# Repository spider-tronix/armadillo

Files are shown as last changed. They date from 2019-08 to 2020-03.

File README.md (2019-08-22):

# armadillo

Design and control of a wheel capable of varying its radius over a range of values using a novel transformation mechanism. The transformation occurs without any additional actuators. Interestingly the wheel can vary its radius ranging from a large diameter to small diameter which enhances its maneuverability like small turning radius and fast/efficient locomotion.

Skeleton view:

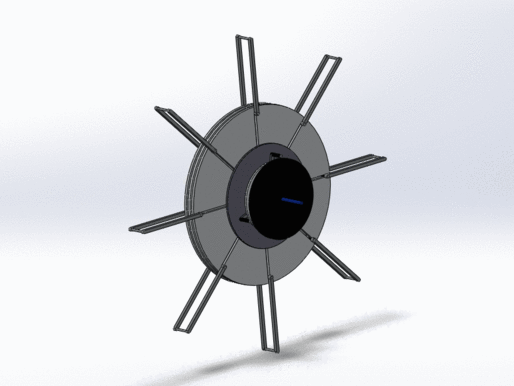
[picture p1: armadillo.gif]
view


Skeleton rear-view:

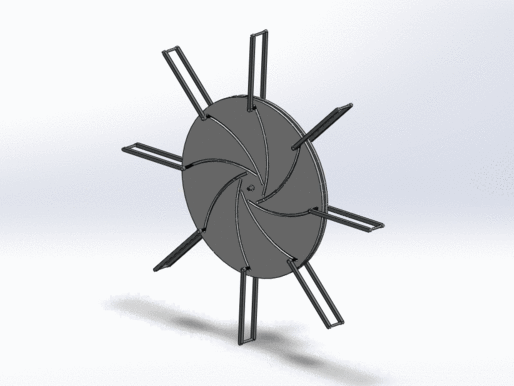
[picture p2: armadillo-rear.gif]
rear-view


The design methodology is explained with much detail in "design.pdf".

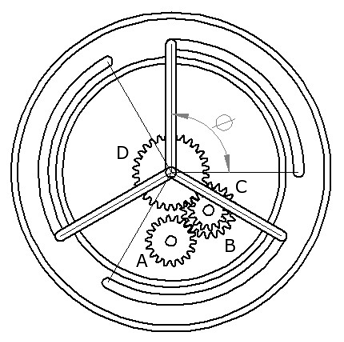
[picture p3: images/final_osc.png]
osc


# Team:
  
  • Mukesh Gandhi [https://github.com/MukkeshGandhi09] 
    
  • Senthur Raj [https://github.com/imsenthur]
  
  • Veejay Karthik [https://github.com/vjkarthik97]
  
  • Soma Karthik [https://github.com/karthiks1701]

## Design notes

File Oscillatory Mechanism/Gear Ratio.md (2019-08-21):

#Oscillatory Mechanism:

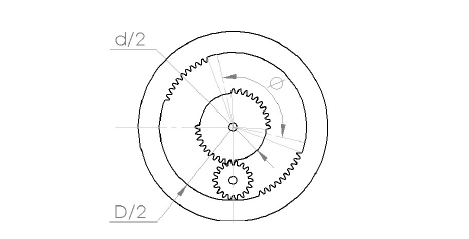
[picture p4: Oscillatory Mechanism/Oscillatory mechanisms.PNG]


The angle of oscillation wrt to inner gear and outer gear is same.

phi*(2d/D-d)=(pi-phi)*(2D/D-d)
phi=pi/(1+(D/d))

    

Ideal Angle of Oscillation
 
Theta=(2d/D-d)*phi
Theta=(2d/D-d)*pi/(1+(D/d))
Theta= 2*pi/(1-k^2)
  
Angle of Oscillation with Clearance 

phi=phi-2*(2*pi/n)
Thetanew= (2/(1-k))*theta
Thetanew=  (2*pi/n)*(n-4(1+k))/(1-k^2)
 
The angle of oscillation is fed to the gear train and Theta max is
obtained

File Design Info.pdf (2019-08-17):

Arc Plate:
Diameter = 160mm
Diameter of arc slots = 3mm
Mass = 63.27 grams
Volume = 63265.19 cubic millimeters
Surface area = 42769.41 square millimeters
Principal axes of inertia and principal moments of inertia: ( grams * square millimeters ) Taken at the center of mass.
Ix = ( 1.00, 0.00, 0.00) | Px = 105645.96
Iy = ( 0.00, 1.00, 0.00) | Py = 105645.96
Iz = ( 0.00, 0.00, 1.00) | Pz = 211162.74
Moments of inertia: ( grams * square millimeters )
Taken at the center of mass and aligned with the output coordinate system. Lxx = 105645.94 Lxy = 0.00 Lxz = 0.00
Lyx = 0.00 Lyy = 105645.97 Lyz = 0.00
Lzx = 0.00 Lzy = 0.00 Lzz = 211162.74
Moments of inertia: ( grams * square millimeters ) Taken at the output coordinate system.
Ixx = 105645.94 Ixy = 0.00 Ixz = 0.00
Iyx = 0.00 Iyy = 105645.97 Iyz = 0.00
Izx = 0.00 Izy = 0.00 Izz = 211162.74

Output shaft:
Diameter = 8mm
Density = 0.00 grams per cubic millimeter Mass = 1.93 grams
Volume = 1926.93 cubic millimeters
Surface area = 1208.18 square millimeters
Principal axes of inertia and principal moments of inertia: ( grams * square millimeters ) Taken at the center of mass.
Ix = ( 0.00, 0.00, 1.00) | Px = 12.45
Iy = ( 0.64, -0.77, 0.00) | Py = 343.81
Iz = ( 0.77, 0.64, 0.00) | Pz = 343.86
Moments of inertia: ( grams * square millimeters )
Taken at the center of mass and aligned with the output coordinate system. Lxx = 343.84 Lxy = -0.02 Lxz = 0.09
Lyx = -0.02 Lyy = 343.84 Lyz = -0.11
Lzx = 0.09 Lzy = -0.11 Lzz = 12.45
Moments of inertia: ( grams * square millimeters ) Taken at the output coordinate system.
Ixx = 3444.88 Ixy = -0.02 Ixz = -0.31
Iyx = -0.02 Iyy = 3444.87 Iyz = 0.38
Izx = -0.31 Izy = 0.38 Izz = 12.45

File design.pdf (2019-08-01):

# Design of a wheel

with dynamically variable curvature.

Rough draft*

Senthur Raj
Department of Production Engineering National Institute of Technology Tiruchirapalli Tamilnadu, India
114116071@nitt.edu

Abstract—This paper presents the design and control of a wheel capable of varying its radius over a range of values using a novel transformation mechanism. The transformation occurs without any additional actuators. Interestingly the wheel can vary its radius ranging from a large diameter to small diameter which enhances its maneuverability like small turning radius and fast/efficient locomotion. Mechanical design of the wheel has been explained in a detailed manner in this paper and also the transforming mechanism and motion study has been shown clearly.
ADD SOME CONTENT HERE

Index Terms—variable radius, maneuverability, locomotion

I. INTRODUCTION

Automobiles are complex machines, in part due to the transmission, suspension,and steering mechanism. By replacing the traditionally static tire with a re-invented wheel that dynamically changes radius, the mechanical complexity of these three systems can be reduced. Reducing the mechanical complexity lowers the cost and required maintenance of a vehicle, all of which are desirable traits for all terrain vehicles and rovers. The design of the wheel consists of three sub-assemblies each of which has dedicated functions to accomplish. The mathematics and working behind each sub-assembly is described in great detail below. INSERT CONTENT HERE !!
Automobiles are complex machines, in part due to the
transmission, | suspension,and | steering | mechanism. | By
replacing the traditionally static tire with a re-invented wheel that dynamically changes radius, the mechanical complexity of these three systems can be reduced. Reducing the mechanical complexity lowers the cost and required maintenance of a vehicle, all of which are desirable traits for all terrain vehicles and rovers. The design of the wheel consists of three sub-assemblies each of which has dedicated functions to accomplish. The mathematics and working behind each sub-assembly is described in great detail below. INSERT CONTENT HERE !!

II. NOMENCLATURE

d | diameter of sun gear
D | diameter of ring gear

D−d
2 | diameter of planet gear

k

d
D
φ | gear mesh angle
n | number of teeth in sun gear
γ | angle of oscillation
θmax | maximum angular displacement of disc
a | radius of inner circle
b | radius of peripheral circle
m | a
| b
A | area of triangle formed by intersection of two circles
L | perimeter of triangle formed by intersection of two circles
r | radial displacement of spokes on wheel
ω | relative angular velocity of disc
t | any instant of time

III. DESIGN METHODOLOGY:
The control of the transformation of wheel is developed in a way to avoid requirement of any additional actuators in order to bring down the hardware complexity. The input shaft when fed with anti-clockwise rotation tends to actuate the transformation mechanism, whereas when fed with clockwise rotation drives the wheel forward. This is type of control over the transformation mechanism is implemented with a trapped one-way bearing,
A. Trapped roller one-way bearing:
A trapped roller one-way bearings is designed to transmit torque between the shaft and housing in one direction and allow free motion in the opposite direction. Proper mounting is easily accomplished with a simple press fit in the casing.

Fig. 1. Trapped roller one-way bearing.

Relative motion between the casing and the input shaft is permitted only when the rotation fed is in clockwise direction. This eliminates any additional actuators required to control the curvature of the wheel.

IV. OSCILLATORY MECHANISM:
The first sub-assembly converts continuous rotation fed in by the input shaft into rotary oscillation of desired angular displacement along the same axis,
A. Gear system that changes direction:

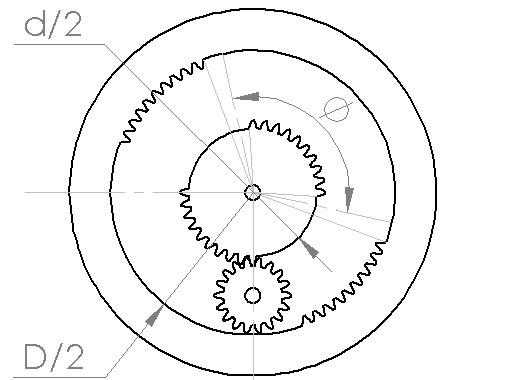
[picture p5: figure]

Fig. 2. Planetary gear assembly.

φ

2d
D−d
= (π −φ)
2D
D−d

φ =

π
(1+k)

(IV-A.1)

B. Angle of oscillation:
The angle of oscillation can be determined as,

γ0 =

2D
D−d
φ

substituting Eq (IV-A.1),

γ0 =

2π
(1−k

2)

the above mentioned angle of oscillation is for an ideal case. While implementation considerations for gear clearance must be made,

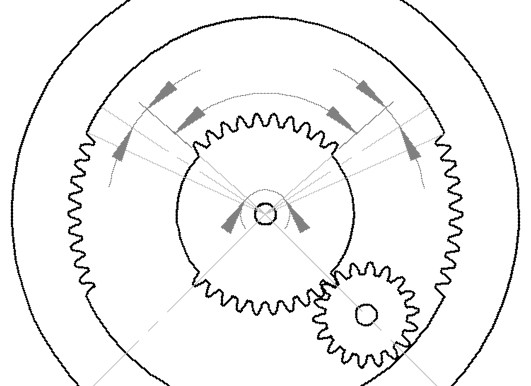
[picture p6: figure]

Fig. 3. Clearance between gears.

therefore, φ = φ −2

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
n−4(1+k)
1−k

2

(IV-B.1)
C. Obtaining the desired angle of oscillation:
The value of θ computed by Eq: (IV-B.1) is completely determined by the ratio of diameters of the sun and ring gears. It is crucial to reduce this value of θ with a gear train in order to reduce the complexity in design of the gear system that changes direction.

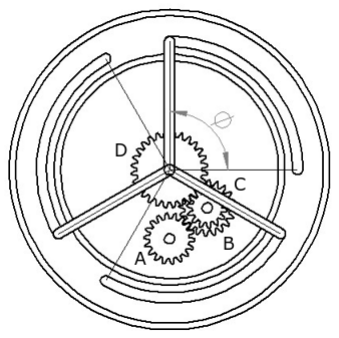
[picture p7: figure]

Fig. 4. Oscillating shaft.

Angle of oscillation of the driver gear (A) is θ which is to be converted into θmax with a compound gear (BC) train with gear ratios,

ratio(AB) =

π

γ

, ratio(CD) =

θmax

π

, ratio(AD) =

θmax

γ

the shaft has three arms, each of which are slotted to prevent overrunning when the driven gear is under clearance angle.

V. EXPANSION MECHANISM:

The expansion mechanism is derived from a self centering mechanism that easily and quickly adjusts to the size of a closed segment ring. This is done by using a pair of disks which rotate against each other, drawing in and out a hex-head nut on a series of opposing arcs. But instead of opposing arcs, the derived system has radial slots in one of the disk opposing the other disc with an arc.

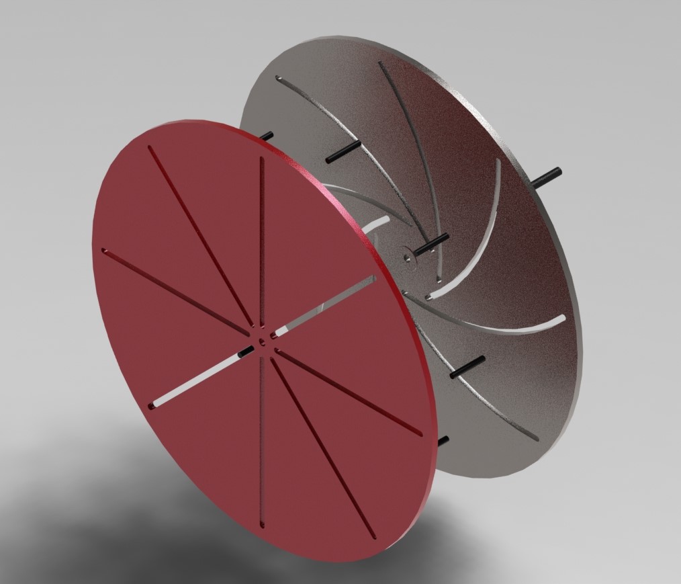
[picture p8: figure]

Fig. 5. Discs and spokes.

A. Locus of the arc:

The arcs on the rotating disc influences the radial expansion of wheel with much impact as they are the driving force behind it. It is important to find their optimal radius of curvature and their corresponding locus assuming center of the shaft as origin.

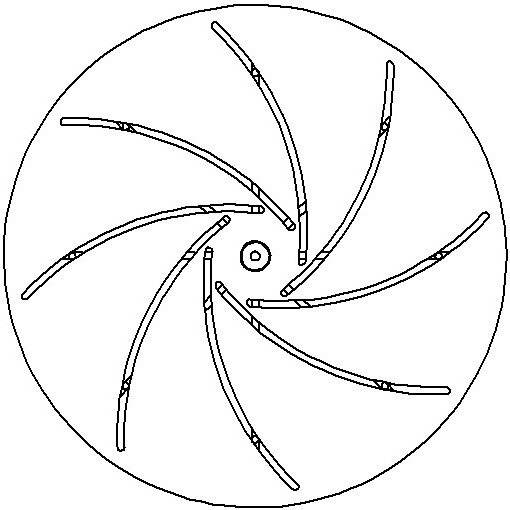
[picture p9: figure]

Fig. 6. arcs.

Locus of the arc is nothing but the intersection of two circles with radii (a + b) and (t) at coordinates (−b,0) and (0,0) respectively. Where (t) is an arbitrary variable.

(x−b)

2 +y

2 = (a+b)

2

x

2 +y

2 | = t
| 2

It is straightforward to show that the intersection of these two circles consists of two points, with the coordinates

x0 =

(−b+0)
2

+

(a+b)

2 −t

2
2L

2

(0−(−b)) +2A
0
L

2

y0 =

(0+0)
2

+

(a+b)

2 −t

2
2L

2

(0) +2A
0−(−b)
L

2

where L is the distance between centers of the two intersecting circles and A is the area of the triangle with edge lengths (a+b), (t), L as given by Herons formula

A =

p
(L+b+a+t)(L+b+a−t)(L+t −b−a)(b+a+t −L) 4

since L = b,

A =

p
(2b+a+t)(2b+a−t)(t −a)(t +a) 4

A =

p
((2b+a)

2 −t

2)(t

2 −a

2)
4

Substituting the values of A and L,

x0 =

−b
2

+

(a+b)

2 −t

2
2b

y0 =

p
((2b+a)

2 −t

2)(t

2 −a

2)
2b

!

Eliminating t, we arrive at locus of the arc,

y

2 | = (a−x)(2b+a+x) | (V-A.1)

where x lies in the domain,
a

2 +2ab−b

| 2
| 2
| <= x <= (a)
B. Polar coordinates:

The locus of arc (Eq:V-A.1) when shifted to polar plane reduces numerous computations during rotation,

x = r cosθ, y = rsinθ

r

2

sin²
θ = (a−r cosθ)(2b+a+r cosθ)

r

2 = 2ab+a 2 −2br cosθ

r =

q
(a+b)

2 −b

2 sin²
θ −bcosθ

where θ lies in the domain,

0 <= θ <= cosh
m

2 +2m−1
2

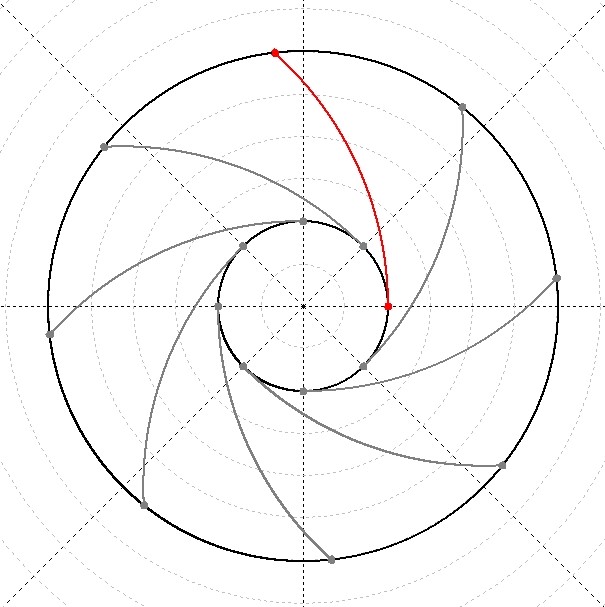
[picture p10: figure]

Fig. 7. Locus of arc.

C. Trajectory of the spoke:

The arcs on the rotating discs determine the curvature of wheel therefore it is crucial to device an equation relating the angular displacement of the disc to the radial expansion of the spokes. Let us consider the trajectory of the spoke which is parallel to x-axis, assuming the spokes are initially at their minimum distance from the origin,

we know that, y = 0 at any point on the trajectory of the above considered spoke and also,

a <= x <= b

Now let us say that the two discs have a relative angular velocity of ω during expansion, at any time t the locus of the arc is given by,

r =

q
(a+b)

2 −b

2 sin²
| (θ −ωt)−bcos(θ −ωt) | (V-C.1)

Trajectory of the spoke in polar coordinates,

rsinθ = 0, | a <= r <= b | (V-C.2)

Computing the intersection of the equations (V-C.1) and (V-C.2) will present us the relationship between the relative angular velocity and the radial expansion of wheel,

rsin(θ −ωt) = 0
=⇒ ωt = θ −nπ

where θ <= cosh
m

2 +2m−1
2
| ,
ωt | = θ

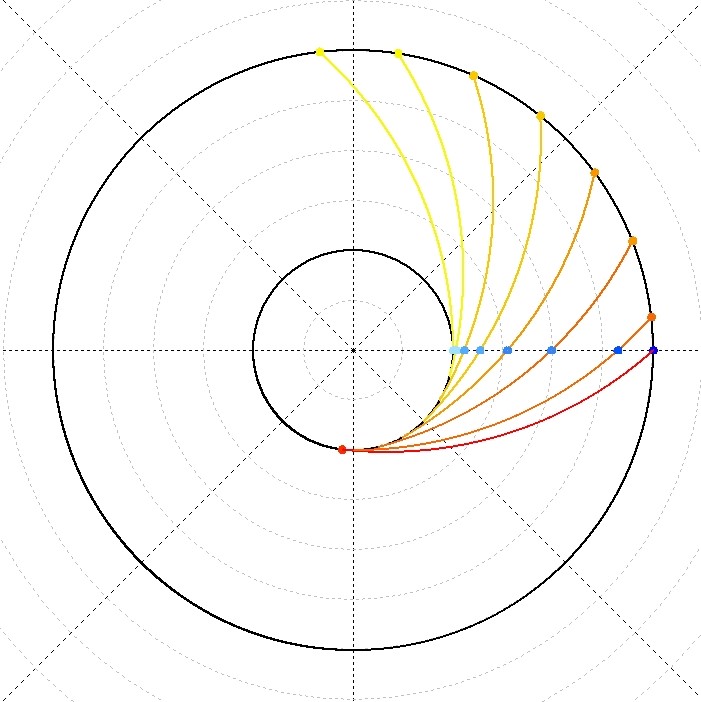
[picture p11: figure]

Fig. 8. Trajectory.

Therefore the angular velocity of the disc and the radial expansion of wheel can be related as,

r =

q
(a+b)

2 −b

2 sin²ωt −bcosωt | (V-C.3)

VI. MOTION STUDY:

A. Rate of expansion:

Now that we have the relationship between angular velocity of the disc and the radial displacement, it is much easier to derive an equation for the rate of expansion. Let us assume at some time t the angular displacement of the disc is θ,

r =

q
(a+b)

2 −b

2 sin²
θ −bcosθ

dr
dt

=

bsinθ −

b

2
cosθ sinθ
q
(a+b)

2 −b
2 sin²
θ

dθ
dt

It is clear that the rate of expansion of the wheel is dependent on the previous state and the angular velocity of the disc.

B. Dependence of ’θmax’ on ’m’:

The dependence of maximum angular displacement of the disc on the ratio of inner and outer radii determines the range over which the curvature of wheel could be varied.
We know that,

θmax = cosh
m

2 +2m−1
2

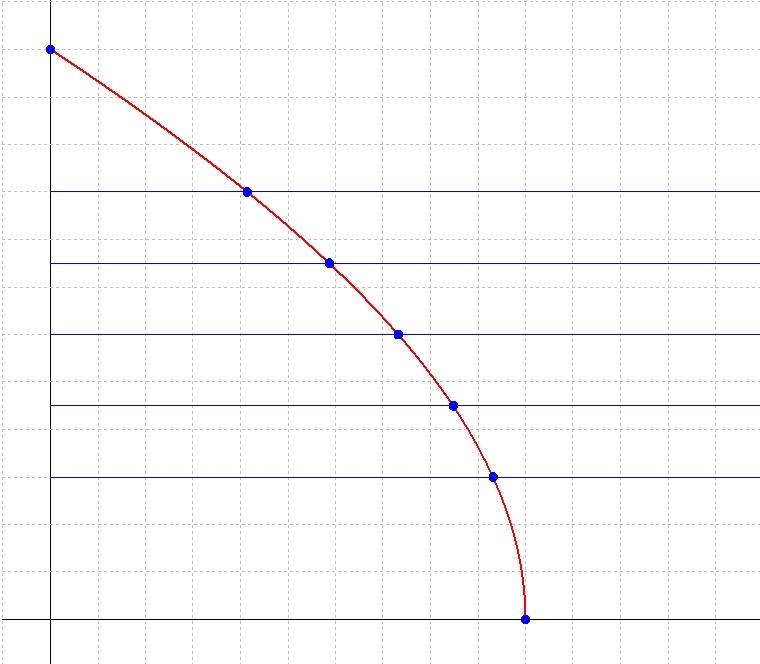
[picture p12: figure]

Fig. 9. θmax vs m.

From the above graph, it is evident that θmax increases with decreasing m, where

0 < m <= 1

also,
−1
2

<

m

2 +2m−1
2

<= 1

0 <= cosh
m

2 +2m−1
2
<

2π
3

=⇒ 0 <= θmax <

2π
3

Therefore θmax ε

0,

2π
3
, though the value of θmax is sub-

jected to change with m it is important to note that it lies well within the constraints posed by the oscillatory mechanism.

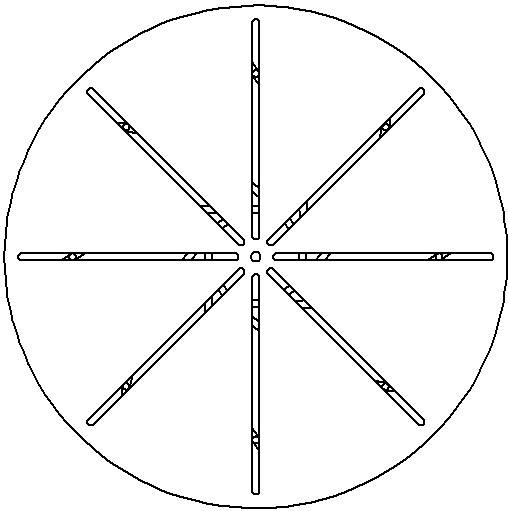
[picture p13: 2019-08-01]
images/faceplate.jpg

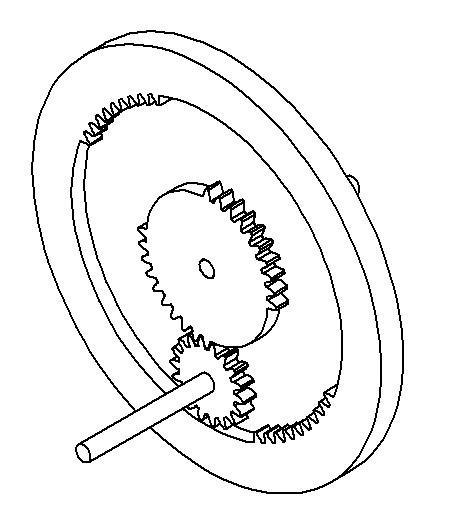
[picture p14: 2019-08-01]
images/mother_child_iso_big.jpg

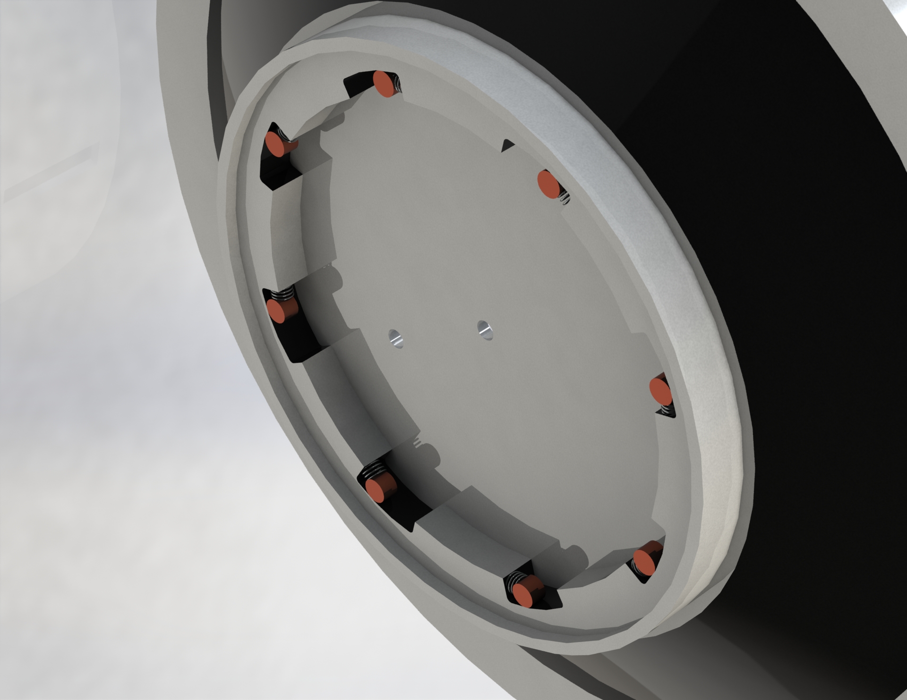
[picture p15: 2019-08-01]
images/trappedRollerBearing.PNG

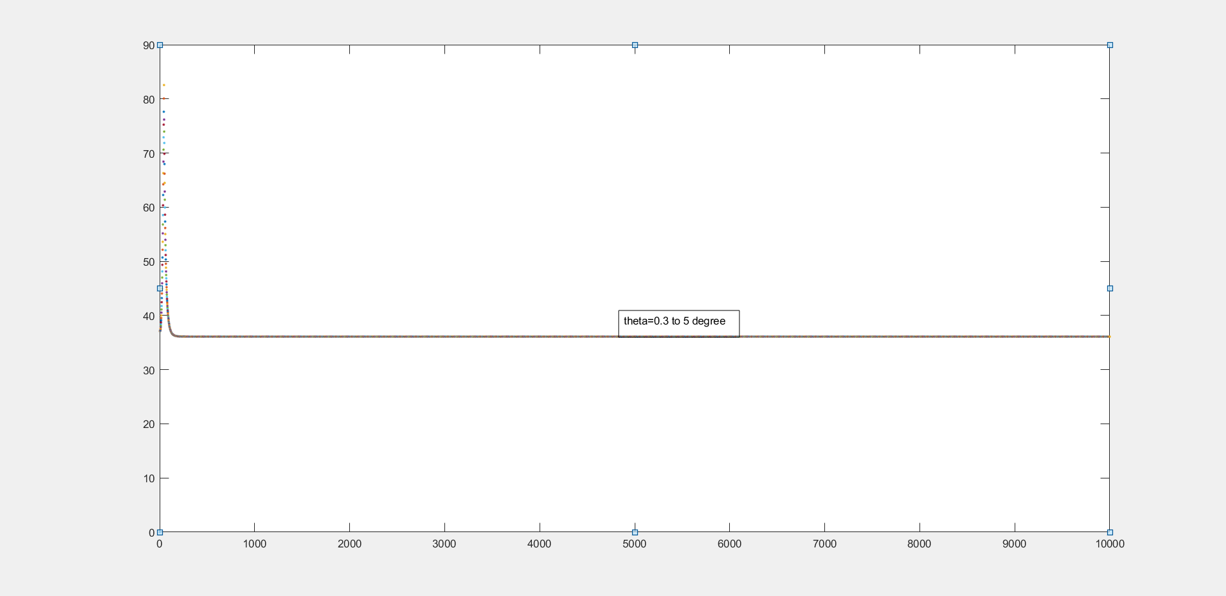
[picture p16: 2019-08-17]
Controller Plots/Higher radius to Lower Radius.png

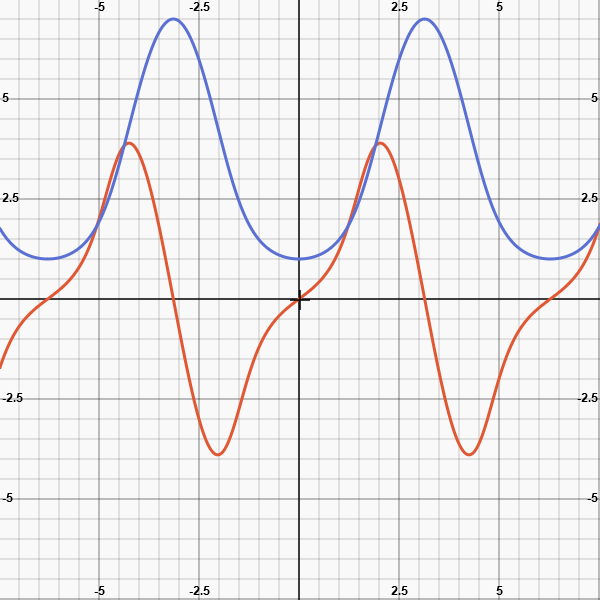
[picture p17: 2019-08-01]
plots/canvas.png

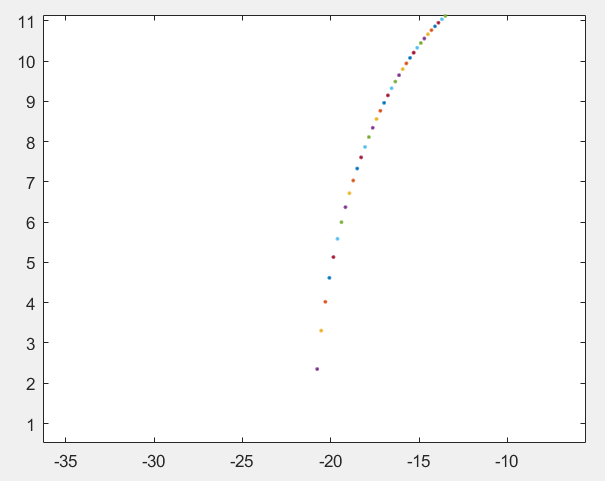
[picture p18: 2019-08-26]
Expansion Mechanism/Plot.PNG

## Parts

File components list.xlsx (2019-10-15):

COMPONENT | REQIREMENT | NO OF PARTS | STATUS
gear box | lasercut | 2 | no
standoff |  |  | no
gear |  | 3 | done
motor |  | 2 | no
coupler |  | 1 | no
gear holder | lasercut | 1 | no
shaft |  | 1
faceplate |  | 1 | done
flange coupling |  | 1 | no
clutch plate |  | 1 | done
spoke |  | 8
idler gear pin |  | 1
actuation shaft |  | 1
casing | 3D print | 1 | no
double bearing | 3D print | 8 | no
bearing |  |  | done
cam | 3D print | 8 | no

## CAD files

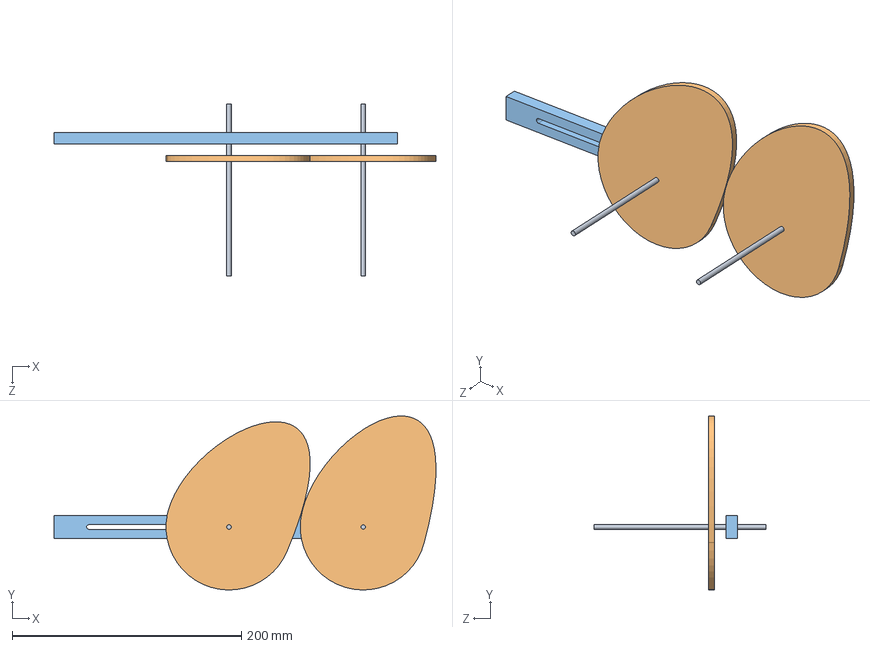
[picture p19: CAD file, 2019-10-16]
new-design/two-spoke-test.SLDASM
333.5 x 151.9 x 150.0 mm
shell-spoke x 2
shell-mockup x 2
mock-spoke-slider

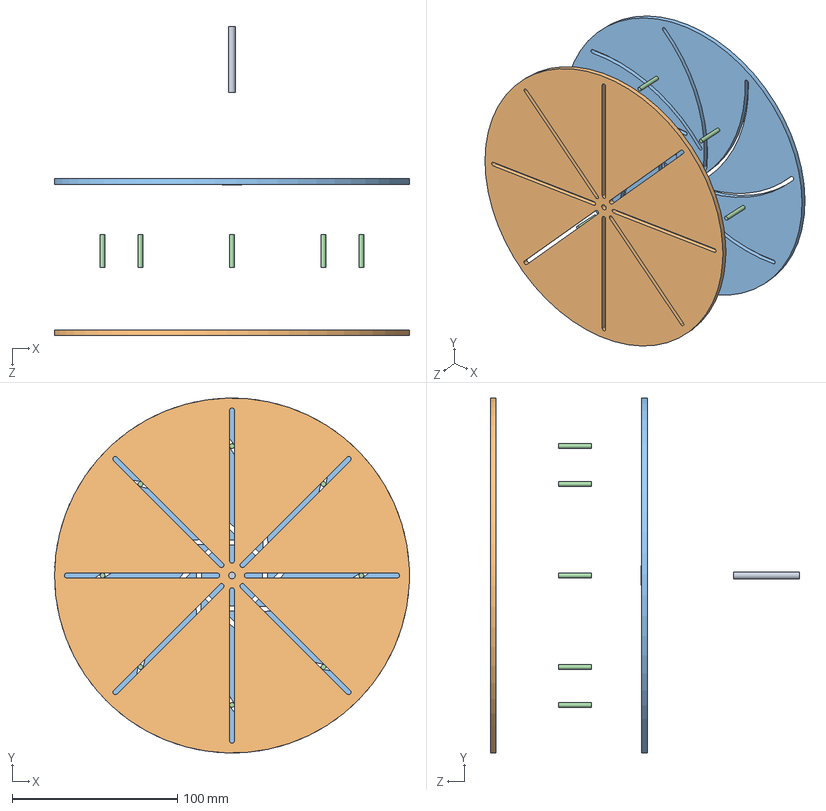
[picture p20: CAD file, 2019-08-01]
subAssemblies/expansion.SLDASM
215.0 x 214.9 x 187.4 mm
shaft_ip
facePlate
clutchPlate
spokes x 8

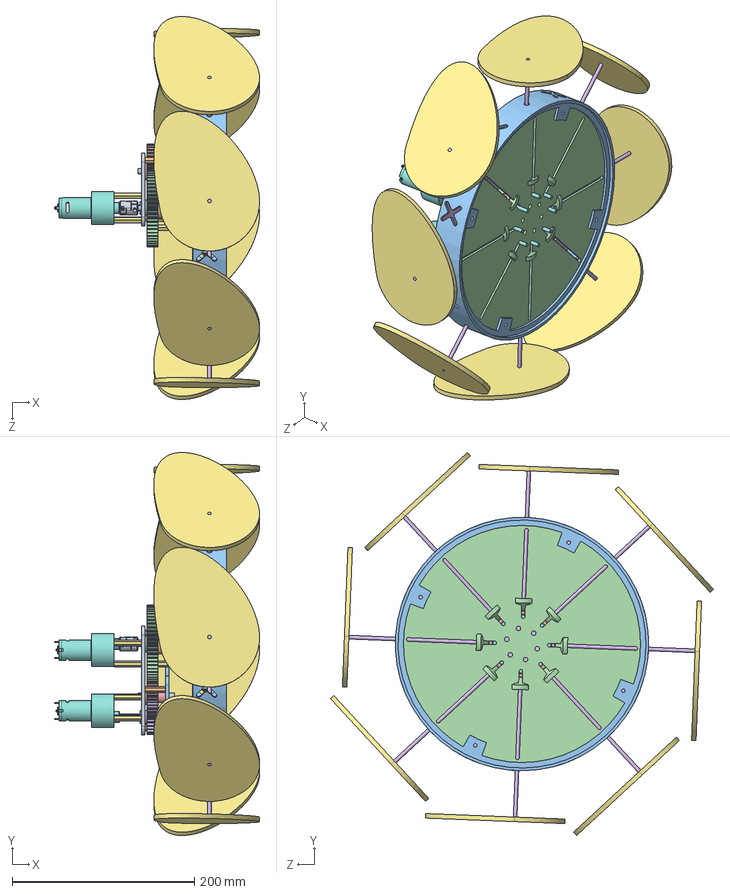
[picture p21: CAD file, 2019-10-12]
new-design/armadillo-assembly.SLDASM
225.1 x 420.1 x 420.1 mm
gear-plate
3mm-standoff x 3
gear-plate-2
56-spur-2
38-spur-2
25-tooth-spur
30mm-3mm-standoff x 6
motor x 2
6mm-coupler
gear-holder
shaft
facePlate-2.0
flange-coupling
clutchPlate-2.0
40MM-3MM-STANDOFF x 3
spoke x 8
idler-gear-pin
actuation-shaft
casing
double-bearing x 8
624RS x 16
shell-spoke x 8
shell-mockup x 8

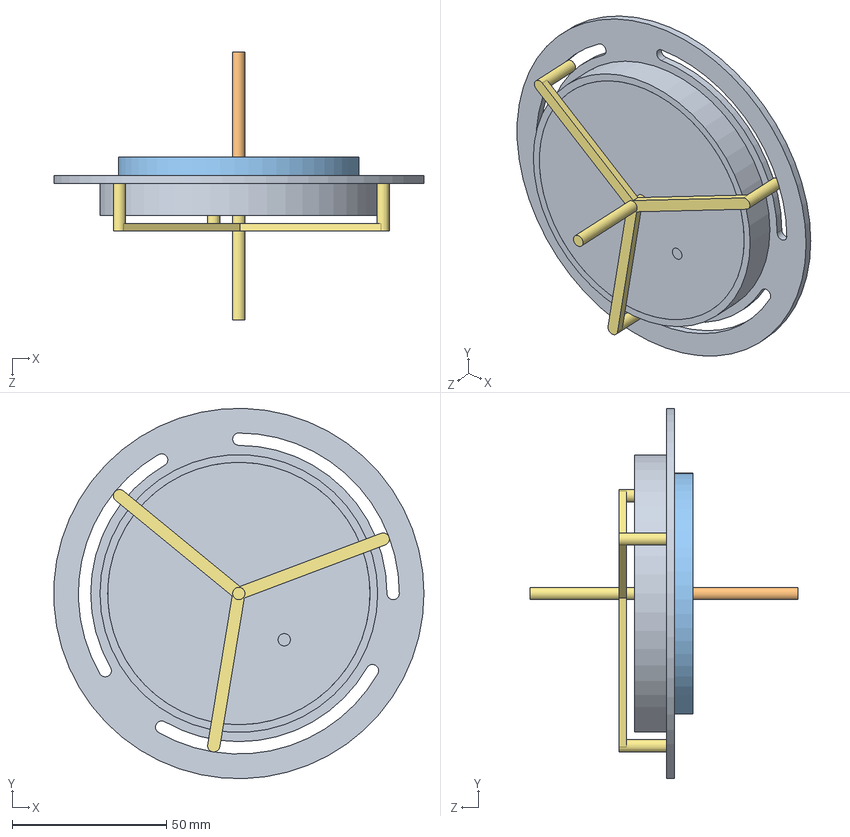
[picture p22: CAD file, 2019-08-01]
subAssemblies/sizeredu_osc_as.SLDASM
119.9 x 119.9 x 86.8 mm
casing
shaft_ip
motherGear_36t72t
childGear_18t x 2
gearPlaceholder
compundGear_20t14t
shaft_op
outSpurGear_28t
enclosingPlate

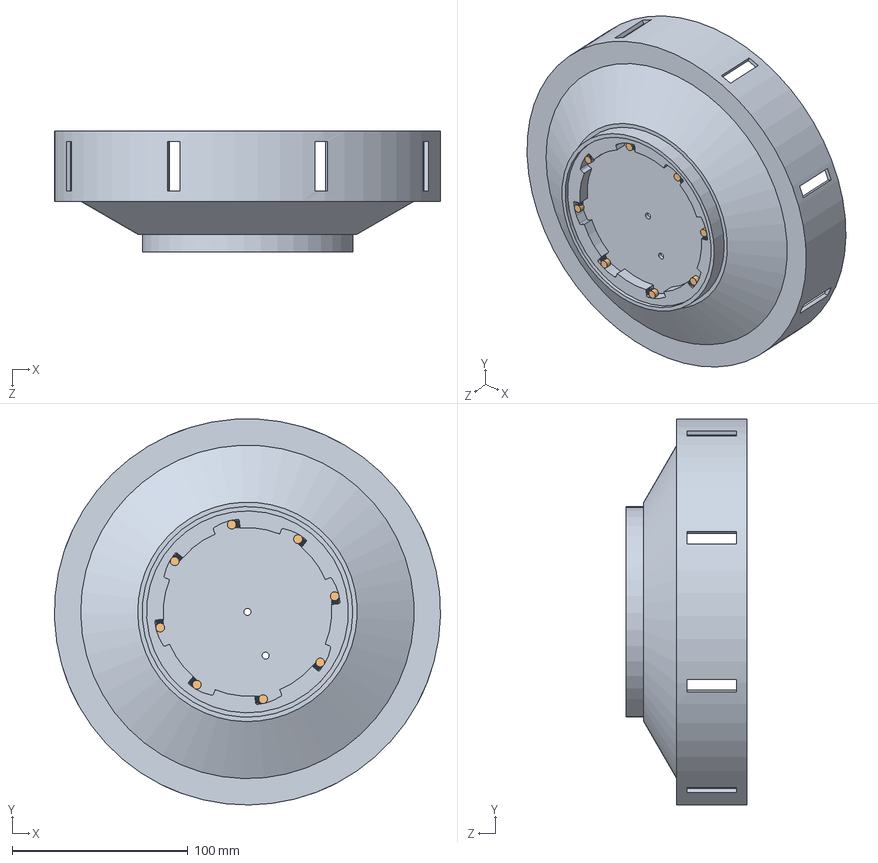
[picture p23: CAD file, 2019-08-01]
subAssemblies/trappedRollerBearing.SLDASM
219.9 x 219.9 x 68.8 mm
casing
trappedRollers x 8
spring x 8

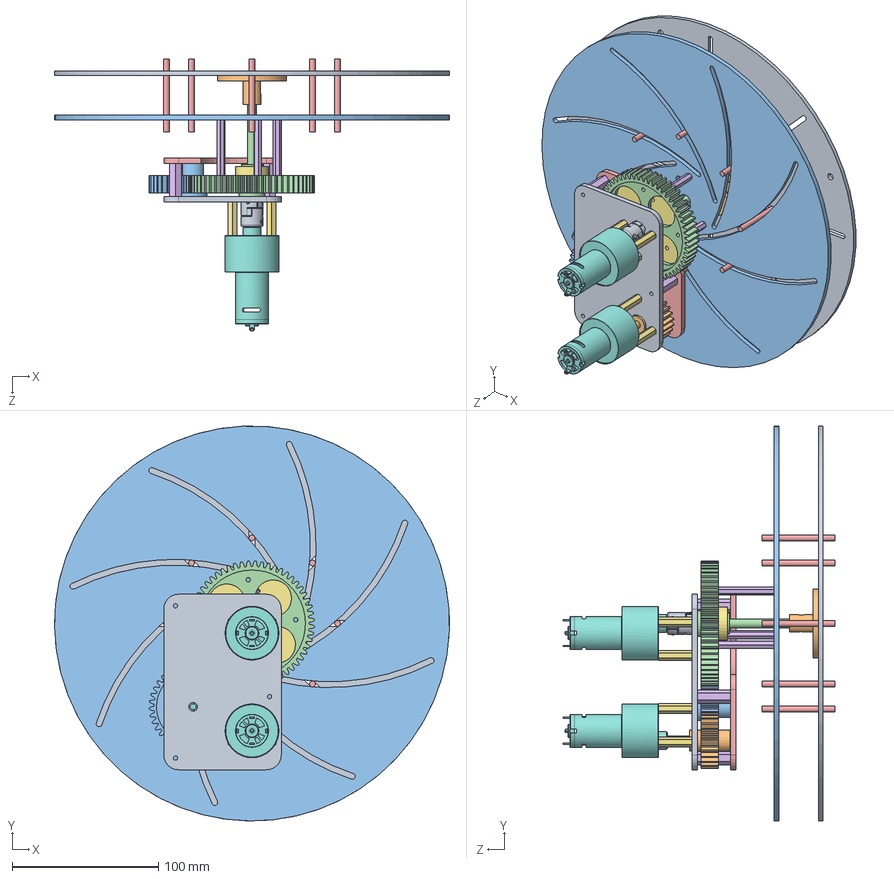
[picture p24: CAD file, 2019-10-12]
new-design/wheel-assembly.SLDASM
270.0 x 269.9 x 186.2 mm
facePlate-2.0
flange-coupling
clutchPlate-2.0
shaft
spoke x 8
TFF-M3x40_DR113.step x 3
gear-holder
idler-gear-pin
gear-plate
25-tooth-spur
38-spur-2
56-spur-2
gear-plate-2
standoff x 3
3mm-standoff x 6
motor x 2
6mm-coupler
actuation-shaft

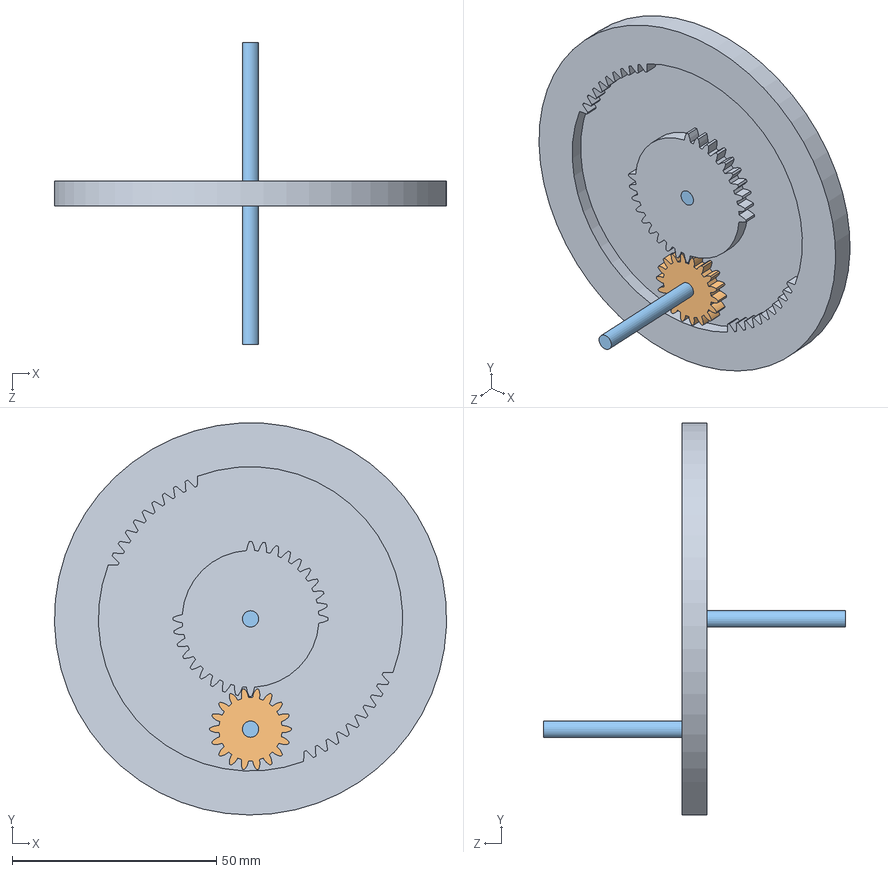
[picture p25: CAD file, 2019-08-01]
subAssemblies/mother_child.SLDASM
96.0 x 95.9 x 74.0 mm
motherGear_36t72t
childGear_18t
shaft_ip x 2

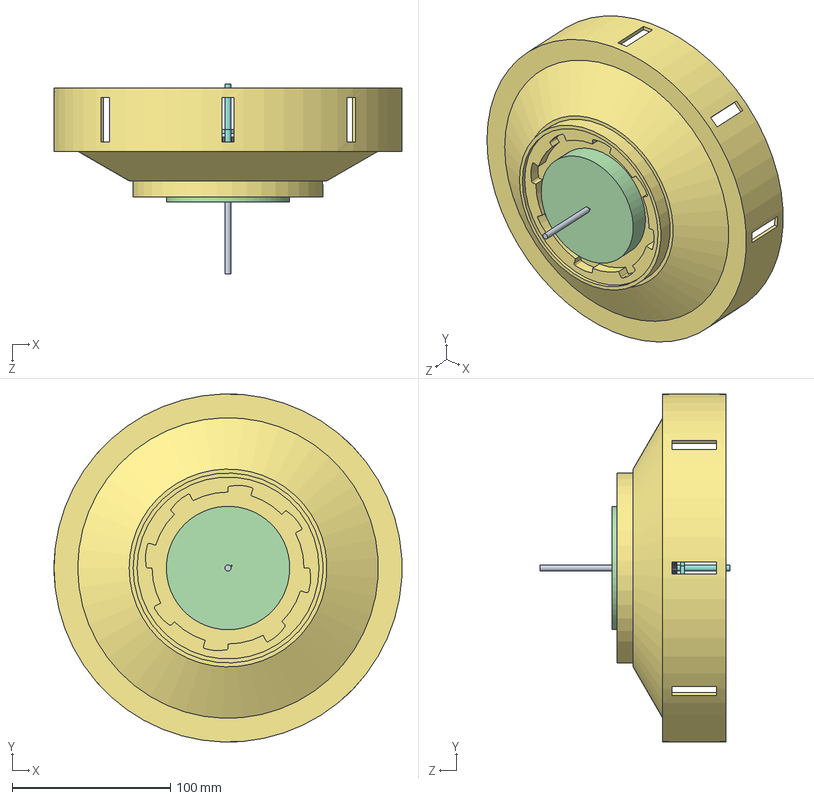
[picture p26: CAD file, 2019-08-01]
subAssemblies/osc_as.SLDASM
219.9 x 219.9 x 120.0 mm
shaft
internalBadassGear x 2
rotationMonitor
mfGear
theOutputGear
theBadassCompoundGear
casing
shaft_op

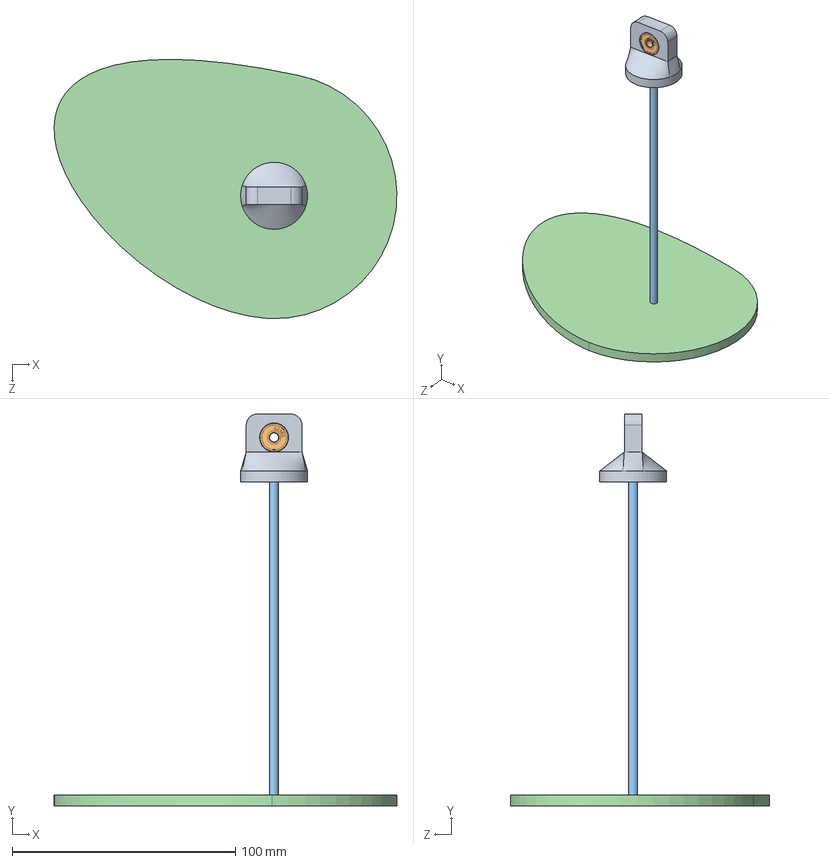
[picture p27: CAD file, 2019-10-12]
new-design/legs.SLDASM
153.5 x 175.5 x 116.1 mm
double-bearing
624RS x 2
shell-spoke
shell-mockup

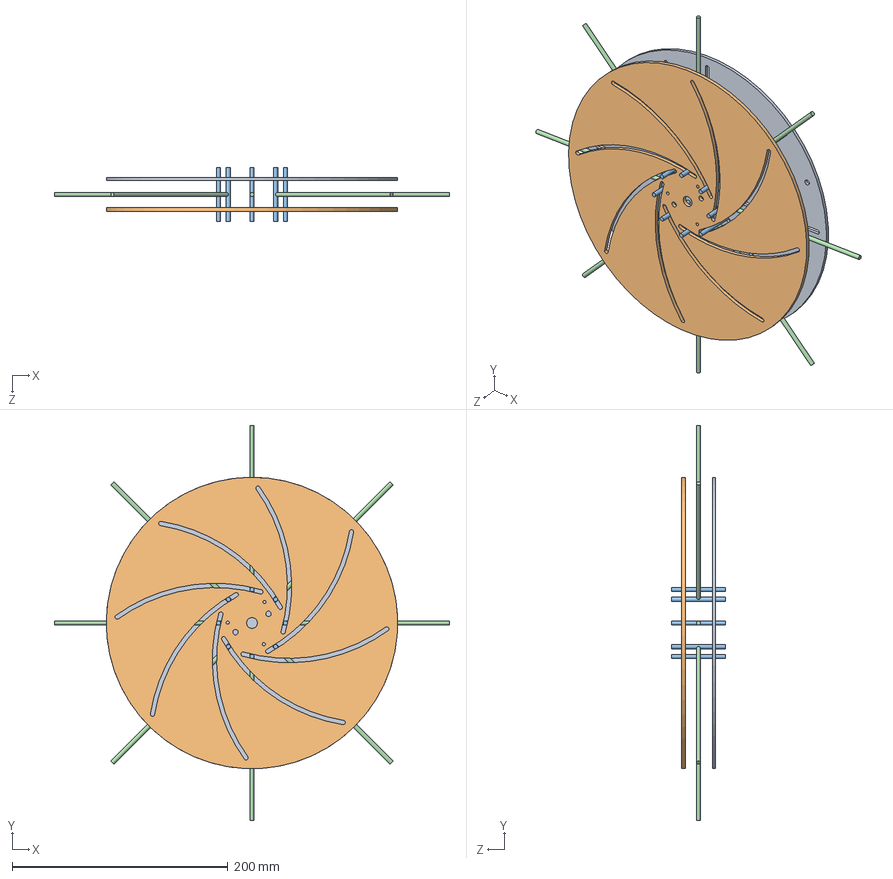
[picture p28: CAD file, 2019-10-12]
new-design/shell-test.SLDASM
365.9 x 365.9 x 50.0 mm
facePlate-2.0
clutchPlate-2.0
spoke x 8
shell-spoke x 8

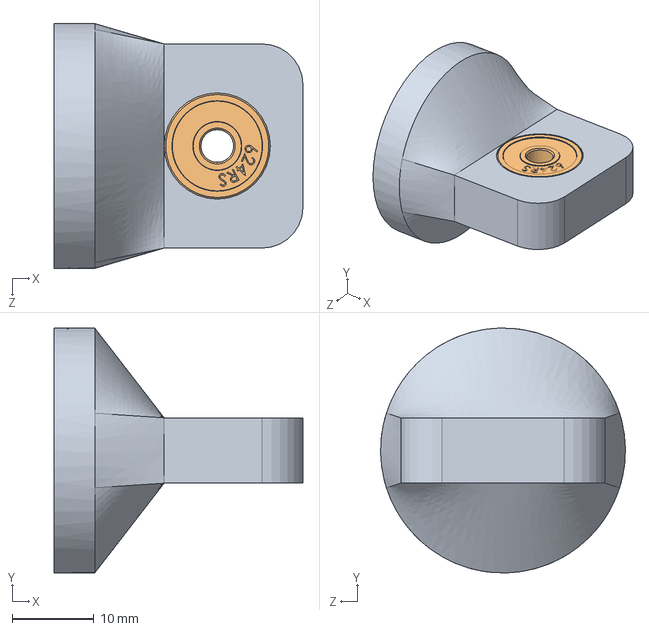
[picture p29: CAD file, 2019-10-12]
new-design/doublebearing.SLDASM
30.5 x 30.0 x 30.0 mm
double-bearing
624RS x 2

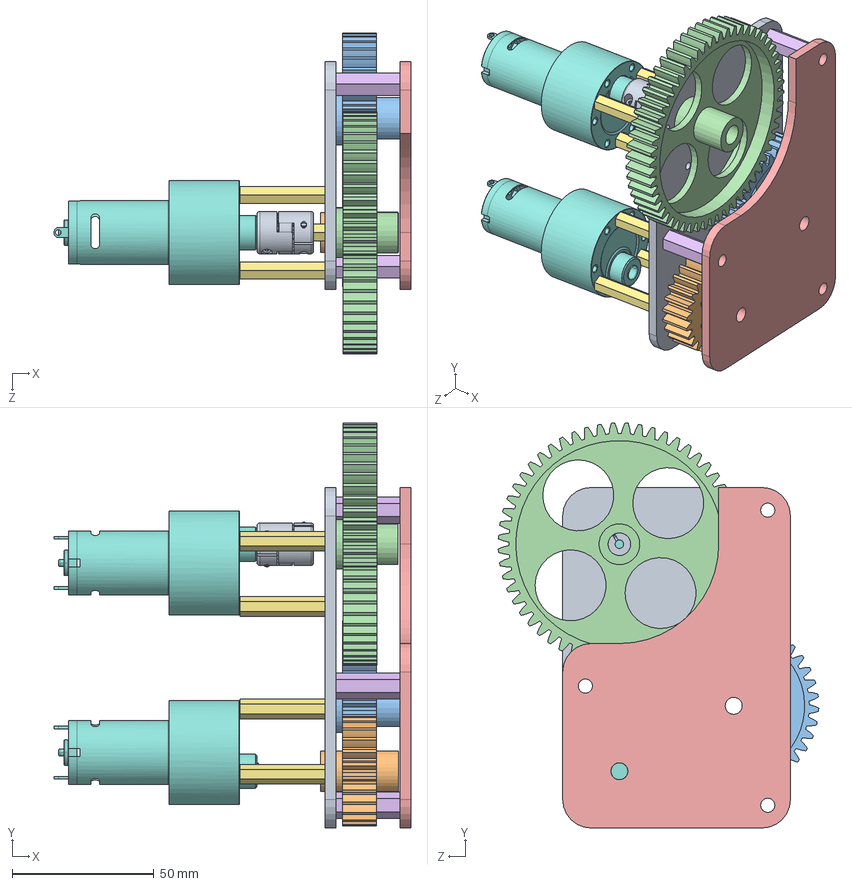
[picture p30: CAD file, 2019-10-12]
new-design/gear-box.SLDASM
125.8 x 142.7 x 113.0 mm
gear-plate
25-tooth-spur
38-spur-2
56-spur-2
gear-plate-2
standoff x 3
3mm-standoff x 6
motor x 2
6mm-coupler

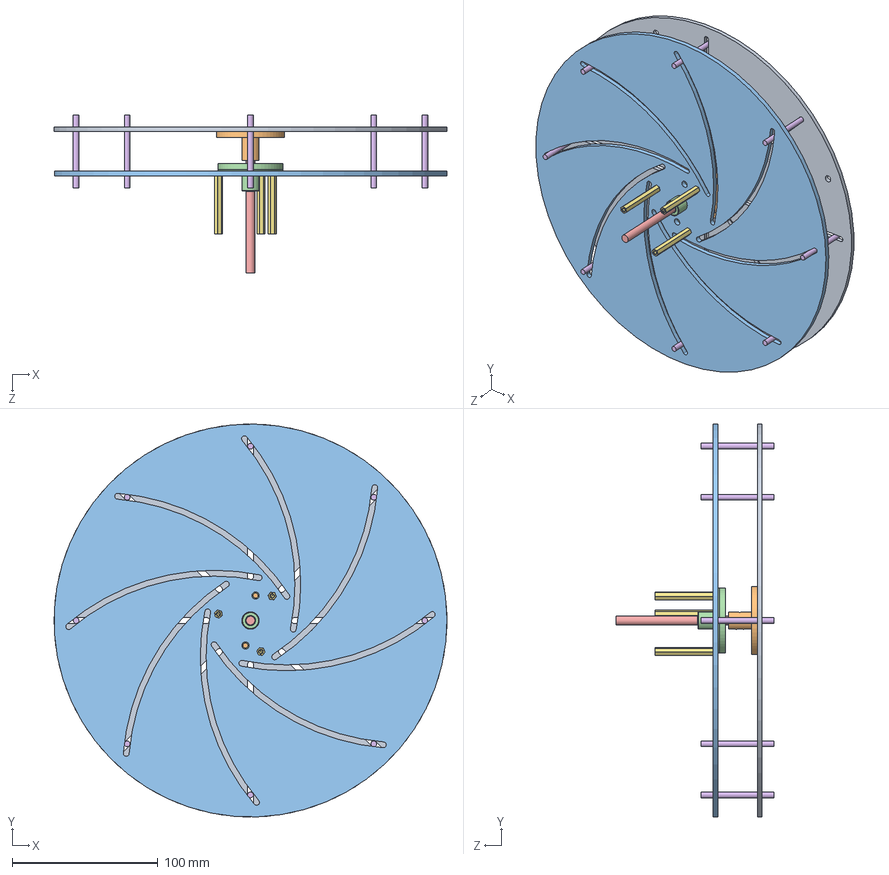
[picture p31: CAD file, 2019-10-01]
new-design/face-clutch-sub.SLDASM
270.0 x 269.9 x 108.2 mm
facePlate-2.0
flange-coupling
clutchPlate-2.0
LMF6
shaft
spoke x 8
TFF-M3x40_DR113.step x 3

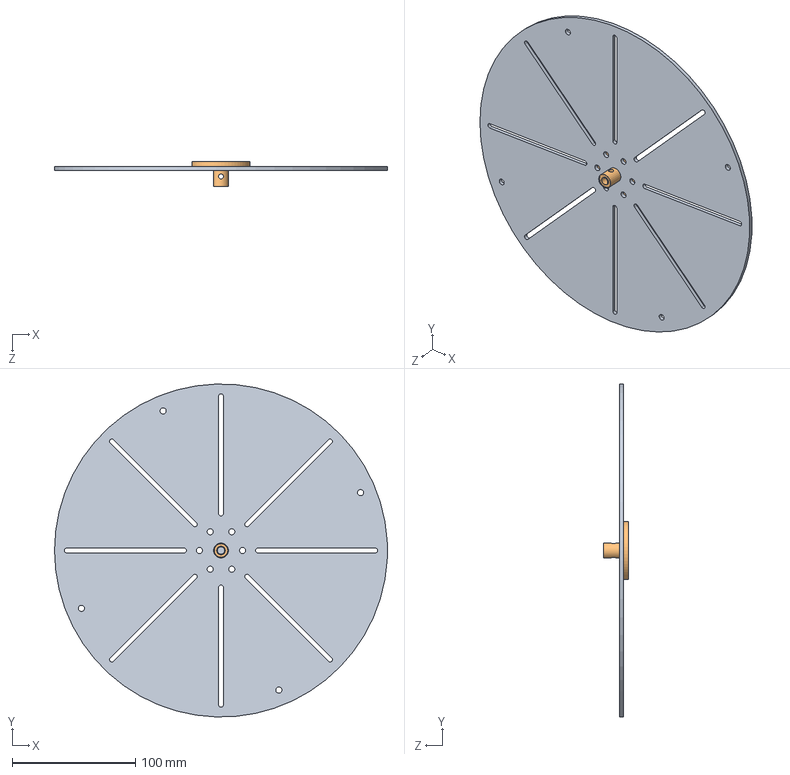
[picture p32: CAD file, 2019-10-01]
new-design/faceplate-sub.SLDASM
270.0 x 269.9 x 20.0 mm
facePlate-2.0
flange-coupling

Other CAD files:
subAssemblies/motionStudy.SLDASM
parts/oscPlate.SLDPRT
parts/childGear_18t.SLDPRT
new-design/40MM-3MM-STANDOFF.SLDPRT
new-design/25-tooth-spur.SLDPRT
new-design/30mm-3mm-standoff.SLDPRT
new-design/38-spur-2.SLDPRT
new-design/3mm-standoff.SLDPRT
new-design/56-spur-2.SLDPRT
new-design/624RS.SLDPRT
new-design/6mm-coupler.SLDPRT
new-design/LMF6.SLDPRT
new-design/actuation-shaft.SLDPRT
new-design/casing.SLDPRT
new-design/clutchPlate-2.0.SLDPRT
new-design/clutchPlate-draw.DWG
new-design/clutchPlate-drawing.SLDDRW
new-design/double-bearing.SLDPRT
new-design/draw.SLDDRW
new-design/facePlate-2.0.SLDPRT
new-design/flange-coupling.SLDPRT
new-design/gear-holder.SLDPRT
new-design/gear-plate-2.SLDPRT
new-design/gear-plate.SLDPRT
new-design/idler-gear-pin.SLDPRT
new-design/motor.SLDPRT
new-design/rim.SLDPRT
new-design/shaft.SLDPRT
new-design/shell-mockup.SLDPRT
new-design/shell-spoke.SLDPRT
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

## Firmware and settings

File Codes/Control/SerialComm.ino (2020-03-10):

boolean motor_start = true;
int factor =10;
const byte pin_a = 2;   //for encoder pulse A
const byte pin_b = 3;   //for encoder pulse B

const byte motordir[2] = {12,13}; 

const byte motorpwm[2] = {5,6}; //for H-bridge: motor speed

int encoder[2] = {0,0};
double pv_speed[2] = {0,0};
double set_speed[2] = {50,50};
double e_speed[2] = {0,0}; //error of speed = set_speed - pv_speed
double e_speed_pre[2] ={0,0};  //last error of speed
double e_speed_sum[2] ={0,0};  //sum error of speed
double pwm_pulse[2] = {0,0};     //this value is 0~255


// -------------------- CASCADED PID PARAMETERS----------------------------//


double delomega_setp = set_speed[0]-set_speed[1];
double delomega_pv = 0;
double e_speed_delomega = 0; //error of speed = set_speed - pv_speed
double e_speed_prev_delomega = 0;  //last error of speed
double e_speed_sum_delomega = 0;  //sum error of speed
double delomegacorrection = 0;     //this value is 0~255

double kpo=0.005,kio=0.05,kdo=0.0;



// ------------------------------------------------------------------------//  



double pv_speedb = 0;
double set_speedb = 60;
double e_speedb = 0; //error of speed = set_speed - pv_speed
double e_speed_preb = 0;  //last error of speed
double e_speed_sumb = 0;  //sum error of speed
double pwm_pulseb = 0;     //this value is 0~255


double kp[2] = {0.9,0.9};
double ki[2] = {0.5,0.5};
double kd[2] = {0.0,0.0};
int timer1_counter; //for timer
int i=0;

void serialEvent() 
{
  char inp;
  while (Serial.available()) 
  {
    inp = (char)Serial.read();
   // Serial.println(inp);
  }

  if( inp == 'w')
  {
    set_speed[0]+=factor;                             // EXPAND 
  }
  else if (inp == 's')
  {
    set_speed[0]-=factor;
  }
  else if (inp == 'e' )
  {
    set_speed[1]+=factor;
  }
  else if (inp == 'd')
  {
    set_speed[1]-=factor;
  }
  else if (inp == 'f')
  {
    Serial.println("Current RPM details");
    Serial.println(pv_speed[0]);
    Serial.println(pv_speed[1]);
    Serial.println("Current Setpoint Details");
    Serial.println(set_speed[0]);
    Serial.println(set_speed[1]);
    
  }

  if( inp == 'b')
  {
    motor_start= false;
    //set_speed[0]=set_speed[1]=0;
    analogWrite(motorpwm[0],0);
    analogWrite(motorpwm[1],0);
    Serial.println("MOTORS STOPPED");
  }
  else if ( inp == 'n')
  {
    motor_start = true;
    Serial.println("MOTORS STARTED");

  }


}

void setup()
 {

  //---------------         //TIMER FUNCTIONS DECLARATIONS 
  noInterrupts();           // disable all interrupts
  TCCR1A = 0;
  TCCR1B = 0;
  timer1_counter = 34286;   // preload timer 65536-16MHz/256/2Hz (34286 for 0.5sec) (59286 for 0.1sec)
  TCNT1 = timer1_counter;   // preload timer
  TCCR1B |= (1 << CS12);    // 256 prescaler 
  TIMSK1 |= (1 << TOIE1);   // enable timer overflow interrupt
  interrupts();             // enable all interrupts
  //---------------

  pinMode(pin_a,INPUT_PULLUP);
  pinMode(pin_b,INPUT_PULLUP);

  for(int i=0;i<2;i++)
  {
  pinMode(motordir[i],OUTPUT);
  pinMode(motorpwm[i],OUTPUT);
  }
  attachInterrupt(digitalPinToInterrupt(pin_a), detect_0, RISING);
  attachInterrupt(digitalPinToInterrupt(pin_b), detect_1, RISING);

  Serial.begin(9600);


 }
 
 
 ISR(TIMER1_OVF_vect)        // interrupt service routine - tick every 0.1sec

 {
  //Serial.println("timer");
  TCNT1 = timer1_counter;   // set timer
  for(int i=0;i<2;i++)
  {
  pv_speed[i] = 60.0*(encoder[i]/3690.0)/0.5;
  //Serial.print("motor");//calculate motor speed, unit is rpm
  //Serial.print(i);
  //Serial.print(" ");
  //Serial.println(pv_speed[i]);
  encoder[i]=0;
 // Serial.print("speed :");
 
  }
  pid();
  
 }

 
 void detect_0()
 {
   encoder[0]++;
 }

void detect_1()
 {
   encoder[1]++;
 }

void loop()
{
  
}

void pid() 

{
  if(motor_start)
  //PID program
   // Serial.print("Relative Omega");
 {
   // Serial.println(pv_speed[0]-pv_speed[1]);
    for(int i=0;i<2;i++)
    {
    e_speed[i] = set_speed[i] - pv_speed[i];
    pwm_pulse[i] = e_speed[i]*kp[i] + e_speed_sum[i]*ki[i] + (e_speed[i] - e_speed_pre[i])*kd[i];
    e_speed_pre[i] = e_speed[i];  //save last (previous) error
    e_speed_sum[i] += e_speed[i];
    }

     // CASCADED PID STATISTICAL APPROACH
    e_speed_delomega=pv_speed[0]-pv_speed[1];
    delomegacorrection=(e_speed_delomega*kpo)+(e_speed_sum_delomega*kio)+((e_speed_delomega-e_speed_prev_delomega)*kdo);
    e_speed_prev_delomega=e_speed_delomega;
    e_speed_sum_delomega += e_speed_delomega;

    if(pv_speed[0]>pv_speed[1])
    {
        pwm_pulse[0]-=fabs(delomegacorrection/2);
        pwm_pulse[1]+=fabs(delomegacorrection/2);
    }
     else if((pv_speed[0]<pv_speed[1]))
     {
        pwm_pulse[0]+=fabs(delomegacorrection/2);
        pwm_pulse[1]-=fabs(delomegacorrection/2); 
     }



  for(int i=0;i<2;i++)
  {
    if (pwm_pulse[i] <255 & pwm_pulse[i] >0)
    { digitalWrite(motordir[i],HIGH);
      analogWrite(motorpwm[i],pwm_pulse[i]);  //set motor speed  
    }
    else
    {
      if (pwm_pulse[i]>255)
      {
        digitalWrite(motordir[i],HIGH);
        analogWrite(motorpwm[i],255);
      }
      else
      {
        digitalWrite(motordir[i],HIGH);
        analogWrite(motorpwm[i],0);
      }
    }

}
 
}
}

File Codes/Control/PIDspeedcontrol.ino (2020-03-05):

boolean motor_start = true;
const byte pin_a = 2;   //for encoder pulse A
const byte pin_b = 3;   //for encoder pulse B

const byte motordir1 = 12; 
const byte motordir2 = 13; 


const byte motorpwm1 = 5; //for H-bridge: motor speed
const byte motorpwm2 = 6; 

int encoder = 0;
int m_direction = 0;
int sv_speed = 100;     //this value is 0~255
double pv_speed = 0;
double set_speed = 0;
double e_speed = 0; //error of speed = set_speed - pv_speed
double e_speed_pre = 0;  //last error of speed
double e_speed_sum = 0;  //sum error of speed
double pwm_pulse = 0;     //this value is 0~255
double kp = 0;
double ki = 0;
double kd = 0;
int timer1_counter; //for timer
int i=0;

void serialEvent() {
  while (Serial.available()) 
  {
    char inp = (char)Serial.read();
    Serial.println(inp)
  }

}

void setup()
 {
  pinMode(pin_a,INPUT_PULLUP);
  pinMode(pin_b,INPUT_PULLUP);
  pinMode(motordir1,OUTPUT);
  pinMode(motordir2,OUTPUT);
  pinMode(motorpwm1,OUTPUT);
  pinMode(motorpwm2,OUTPUT);
  attachInterrupt(digitalPinToInterrupt(pin_a), detect_a, RISING);
  attachInterrupt(digitalPinToInterrupt(pin_b), detect_b, RISING);
  // start serial port at 9600 bps:
  Serial.begin(9600);
  //--------------------------timer setup
  noInterrupts();           // disable all interrupts
  TCCR1A = 0;
  TCCR1B = 0;
  timer1_counter = 59286;   // preload timer 65536-16MHz/256/2Hz (34286 for 0.5sec) (59286 for 0.1sec)
  TCNT1 = timer1_counter;   // preload timer
  TCCR1B |= (1 << CS12);    // 256 prescaler 
  TIMSK1 |= (1 << TOIE1);   // enable timer overflow interrupt
  interrupts();             // enable all interrupts
  //--------------------------timer setup
 }

 void detect_a()
 {
   encoder++;
 }
̥
 void detect_b()
 {

 }

 ISR(TIMER1_OVF_vect)        // interrupt service routine - tick every 0.1sec
{
  Serial.println("MUKESHHHHH")
  TCNT1 = timer1_counter;   // set timer
  pv_speed = 600.0*(encoder/200.0)/0.1;  //calculate motor speed, unit is rpm
  encoder=0;
  //print out speed
  //if (Serial.available() <= 0) {
  //Serial.print("speed");
  // Serial.println(pv_speed);         //Print speed (rpm) value to Visual Studio
 }

void loop() 

{
  //PID program
  if (motor_start){
    e_speed = set_speed - pv_speed;
    pwm_pulse = e_speed*kp + e_speed_sum*ki + (e_speed - e_speed_pre)*kd;
    e_speed_pre = e_speed;  //save last (previous) error
    e_speed_sum += e_speed; //sum of error
    if (e_speed_sum >4000) e_speed_sum = 4000;
    if (e_speed_sum <-4000) e_speed_sum = -4000;
  }
  else{
    e_speed = 0;
    e_speed_pre = 0;
    e_speed_sum = 0;
    pwm_pulse = 0;
  }
  
  //update new speed
  if (pwm_pulse <255 & pwm_pulse >0){
    analogWrite(pin_pwm,pwm_pulse);  //set motor speed  
  }
  else{
    if (pwm_pulse>255){̥
      analogWrite(pin_pwm,255);
    }
    else{
      analogWrite(pin_pwm,0);
    }
  }
  
}

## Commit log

2019-08-01 Individual parts constituting the wheel.
    [casing.SLDPRT, childGear_18t.SLDPRT, clutchPlate.SLDPRT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]
2019-08-01 Sub-assemblies added.
    [entireAssembly.SLDASM, expansion.SLDASM, mother_child.SLDASM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]
2019-08-21 Gear Ratios
2019-08-21 Rename Gear Ratio to Gear Ratio.md
2019-08-21 Corrected gear Ratio
2019-08-22 Fixed broken assembly and obtained GIFs.
    [casing.SLDPRT, childGear_18t.SLDPRT, clutchPlate.SLDPRT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]
2019-09-19 Modified plates to accomodate flange coupling/bearing.
    [clutchPlate-2.0.SLDPRT, facePlate-2.0.SLDPRT, faceplate-sub.SLDASM]
2019-09-19 Flange-bearing (6mm)
    [LMF6U.SLDPRT]
2019-09-19 Flange-coupling (6-47-19mm)
    [flange-coupling.SLDPRT]
2019-09-19 Plates sub-assembly (spoke+shaft+coupling+bearing)
    [face-clutch-sub.SLDASM, shaft.SLDPRT, spoke.SLDPRT]
2019-09-24 Modified plates for fabrication.
    [clutchPlate-2.0.SLDPRT, face-clutch-sub.SLDASM, facePlate-2.0.SLDPRT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]
2019-09-27 Output circuit Simulation
2019-10-01 added gear design
    [25-tooth-spur.SLDPRT, 38-spur-2.SLDPRT, 56-spur-2.SLDPRT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]
2019-10-02 Actuation shaft and gear-holder.
    [actuation-shaft.SLDPRT, gear-holder.SLDPRT, idler-gear-pin.SLDPRT]
2019-10-02 Added material-props.
    [25-tooth-spur.SLDPRT, 38-spur-2.SLDPRT, 56-spur-2.SLDPRT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]
2019-10-02 Wheel-assembly (plates/gearbox/shaft)
    [spoke.SLDPRT, wheel-assembly.SLDASM]
2019-10-03 Added motor-model (shadow).
    [motor.SLDPRT]
2019-10-10 Output PCB layout
2019-10-10 Shell-locus test script (mock-up).
    [clutchPlate-2.0.SLDPRT]
2019-10-10 Added mock-up files for shell-test (.sldprt)
    [shell-mockup.SLDPRT, shell-spoke.SLDPRT]
2019-10-10 TEST 1: FAIL, should re-work the expansion-continuity.
    [shell-test.SLDASM]
2019-10-11 Modified face-plate-2.0
    [facePlate-2.0.SLDPRT]
2019-10-11 Added gear-box support files.
    [3mm-standoff.SLDPRT, 56-spur-2.SLDPRT, 6mm-coupler.SLDPRT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]
2019-10-12 added final assembly
    [25-tooth-spur.SLDPRT, 30mm-3mm-standoff.SLDPRT, 38-spur-2.SLDPRT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]
2019-10-14 added components list
    [components list.xlsx]
2019-10-15 A new take on the pressure/normal angle at POC.
2019-10-16 Two-spoke planar assembly for testing cam-follower.
    [two-spoke-test.SLDASM]
2019-10-17 PWM for Matlab interface
2019-10-18 Manual tuning old motor
2019-10-18 PID simulink model
2019-10-22 RMCS Arduino Library
2019-10-23 Position+Velocity initiated
2019-11-04 Motor-driver Documentation
2020-03-05 Cascaded pid init
2020-03-05 Cascaded PID check
